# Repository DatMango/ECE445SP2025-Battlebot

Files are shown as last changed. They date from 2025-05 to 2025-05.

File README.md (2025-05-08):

# ECE445SP2025-Battlebot
UIUC ECE 445 Spring 2025 - Senior Design Repository

## Project: Ant-weight, 3D Printed Battlebot
Name of Battlebot: Ant-weight Battlebot - Scooper

<p align="center">
    Scooper Image
</p>

## Team Members:
- Justin Leong (jyleong2@illinois.edu)
- Yuxuan Nan (yuxuann2@illinois.edu)
- Zilong Jiang (zjian4@illinois.edu)

## TA:
- Bill Yang (hy38@illinois.edu)

## Problem
The issue at hand is an Ant-weight, 3D Printed Battlebot Competition in which each team wants to win. There are certain constraints of the Battlebots’ design in order to be eligible and win. To win the competition, the goal of a battlebot is to outlast or destroy the opponent team’s battlebot. Different teams will have different designs, meaning a battlebot designed for winning must take into account as many factors to withstand and outlast the competition.

## Solution
We decided upon developing a 3D Printed Bluetooth-controlled battle bot powered by an ESP32 microcontroller. The Battlebot communicates with a PC via a Bluetooth module, enabling wireless command and control. It is equipped with two DC motors driven by H-bridge circuits for precise movement and a ramp-shaped weapon system for engaging in battles. The ESP32 manages motor control using GPIO and PWM, while the weapon system utilizes GPIO. The bot integrates real-time communication, robust motor control, and weapon functionality, offering an engaging and functional design. My goal is to create a responsive and competitive robot for dynamic competitions.

## Lab Notebook
[Can be found here!](Documentation/Notebook.md)

## Video!
[Battlebot Intro Video](https://youtu.be/LQH7uXVlK6E)

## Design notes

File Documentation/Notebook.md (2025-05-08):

# Lab Notebook
For weekly entries of what occurred in design.

Our weekly meetings with our TA, Bill Yang, were on Mondays 6-6:30PM.

### Final Design
<p align="center">
    Final Battlebot Image
</p>

# Week of Jan 20
The beginning of the school year, formed group of: Justin, Yuxuan, and Zilong. This was the week of the Initial Web Board Post. Also when we decided on the idea of partaking in the Antweight, 3D Printed Battlebot competition hosted by Professor Gruev.

# Week of Jan 27
Our group solidifed of taking the Antweight Battlebot competition, and created our Early Project Approval to turn in 1/29. Everyone worked together to make sure to include the necessary details for the Early Project Approval ([Early RFA](Early%20RFA.md)). Also the week of the CAD assignment.

# Week of Feb 3
After third class meeting, we confirmed together that we were working on the Antweight Battlebot. Also were confirmed to be the first group to be approved - hence became Group 1. We began working together on the Project Proposal.

# Week of Feb 10
This week contained our first meeting with our TA (Bill). Beforehand, we as a team had prepared and worked on a first draft of our Block Diagram, three High-Level Requirements, and one Subsystem Requirement from our worked on Project Proposal. We had seeked feedback from Bill upon our project and got some guidance in the right direction on how to develop a Pneumatic system. We also sought advice on if we were in the right direction for our Project Proposal. This was also the week we turned in our [Project Proposal](Project%20Proposal.pdf) as well as our [Team Contract](Team%20Contract.pdf). Finally, we made sure that our Project Proposal was ready for the Proposal Review.

### Images
<p align="center">
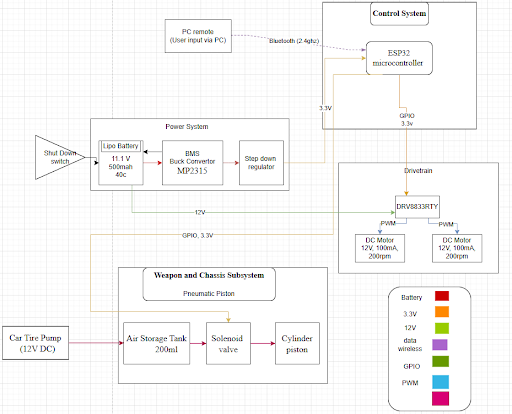
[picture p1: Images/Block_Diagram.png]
Final Block Diagram
    
</p>

# Week of Feb 17
No weekly meeting with Bill this week. There would be a Design Review of our Project Proposal. Design Review would take place on 2/19 11AM. I believe there was an update to our high level block diagram a day before the review due to some missing parts.

### Tasks
- Everyone focuses on making sure [Project Proposal](Project%20Proposal.pdf) was ready for the Project Proposal / Design Review.
- Begin on working on PCB schematics.

# Week of Feb 24
Our weekly meeting with our TA is now Mondays 6-6:30pm. Feedback from Bill for this week was primarily about looking at our PCB schematics but this was when we had the STM32. Partial of the STM32 wiring can be found in the images section. We also did ask about changing from STM32 to ESP32 but this would later be done after the PCB Review. After the PCB Review, we were told that we were allowed to change from STM32 to ESP32. The STM32 we had originally picked did not support Bluetooth or WiFi communications, additionally, we found the ESP32-WROOM-32E to be easier to work with and supported all of our needs. We would also try to finish the PCB files before the first round PCBway orders. We also began working on the Design Document. Towards the end of the week after deciding to swap to the ESP32, we also began figuring out how to code for the ESP32 using WiFi signals as originally (Justin) thought that WiFi would be more instant than Bluetooth. However, later on we learned the actual difference between Bluetooth and WiFi is quite minimal for these kinds of projects in comparison to things that require 2.4Ghz connections (i.e. Gaming/Reaction based projects).

### Images
<p align="center">
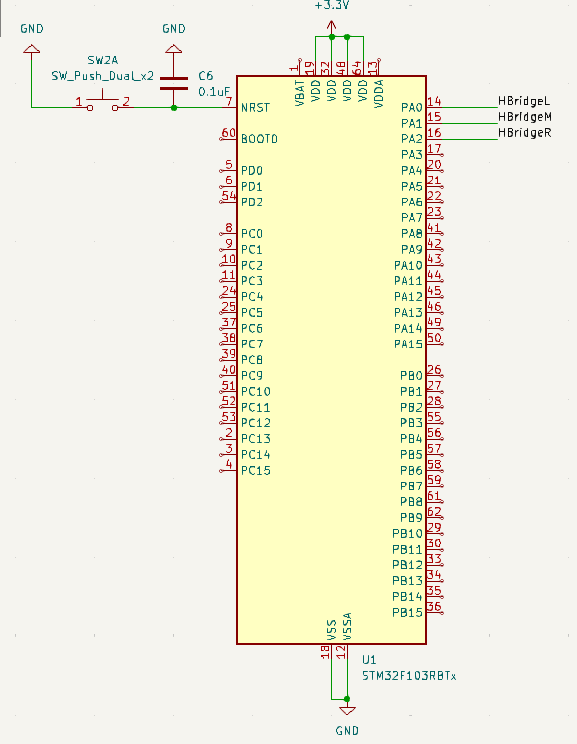
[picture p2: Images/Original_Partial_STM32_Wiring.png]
Partial STM32 Wiring
    
</p>

### Tasks
- Everyone begins working on PCB schematic and layout
- Everyone Research parts (datasheets) required for system to better understand PCB
- Everyone also work on the Design Document
- Zilong will be focusing on researching Pneumatics and schematics
- Justin and Yuxuan will be focusing on the software/programming of the ESP32, test on dev kit

# Week of Mar 3
Unfortunately, we did not finish all of the PCB schematics before the first round PCBway orders which was due during our TA meeting. This was primarily due to having to rewire components and read the datasheet of the ESP32 we picked. However, we did ask Bill more in depth questions about if what we were doing for our schematics and PCB design were good or not. We got feedback of how we could utilize the datasheets of components to easily wire everything. In terms of coding a frontend, we also asked Bill on some advice with coding our controller on PC using things like the Python library Tkinter and other frontends. During this week, we all also had to work on and turn in the [Design Document](Design%20Document.pdf). For the Design Document, also decided that we wouldn't use a step down regulator as the Buck Converter was able to change the 12V to 3.3V voltage on its own safely. Finally, Justin and Yuxuan would get ready for the Breadboard Demo by programming the ESP32 and connecting to our PC (as controller) over WiFi (hotspot) and getting some signals to work.

### Tasks
- Everyone prepare for Breadboard demo
- Everyone will work together on PCB design, primarily Zilong 
- Everyone finish the [Design Document](Design%20Document.pdf)
- Everyone get ready to order parts (pick and choosing), Yuxuan will handle most of the ordering
- Justin and Yuxuan focus on getting the ESP32 programmed (using WiFi) with a frontend controller on PC

# Week of Mar 10
No weekly TA meeting this week. For the Breadboard Demo, we were able to get a version running where we could send either 1 or 5 signals to our ESP32 and get outputs (LEDs) on the breadboard to work. However, the 5 signal version didn't work very well. From the Breadboard demo with Professor Gruev and TA Bill, we were told that we were a bit behind schedule (compared to other teams). Additionally, this was when Professor Gruev helped us make the decision of switching back from WiFi to Bluetooth because there were still secure connections over Bluetooth and reduces points of failures. 

We also finished our first revision of our PCB for the second round PCBway orders. We made sure to design our PCB utilizing the datasheets of components. Important components like the LM2596S-3.3 buck converter, power switch, ESP32-WROOM-32E microcontroller, DRV8833RTY H-Bridge module. Converted to [Gerber V1](../PCB/Gerber%20V1/) files. We also started purchasing some components.

For the coding portion: Essentially, we used a hotspot (WiFi) as our method of wireless communication for this week as it seemed more instant. Additionally, we chose hotspot due to some restrictions from the school's internet. Furthermore, we were able to get our Devkit to connect to our hotspot and computer, thus allowing for signals to be sent back and forth. We designed an interface with 5 on-screen buttons (on/off) that were mapped to specific GPIO pins (programmed) through Arduino IDE. To make sure we were sending signals properly, we connected LEDs to each of the GPIO pins programmed to see whether they could be turned on/off. The 1 version button was fine, but when changing to 5 buttons, there were some weird issues with it that we attempted to debug.

### Tasks
- Justin and Yuxuan primarily focus on getting programming done for the Breadboard Demo
- Everyone focus on getting in our PCB Design in for PCBway orders, everyone helps with schematic
- Zilong will get the PCB layout designed with assistance from Yuxuan

### Notes
- Code that we utilized for this Breadboard demo can be found in [Old Code, connected utilizing WiFi/HotSpot](../Code/Original%20Code%20(Not%20Working)/)
- The portions of our original PCB design that we used can be found in [Design Document](Design%20Document.pdf). The actual Gerber files (that we still have) can be found in [PCB Gerber Rev 1 Files](../PCB/Gerber%20V1/)
- An example of issues we ran into for our Revision 1 PCB is in the Images

### Images
<p align="center">
    Rev1 PCB Error
</p>

# Week of Mar 17
The week of spring break. Attempt to get back on schedule if time. Ordered some components. Found Dabble library to utilize for controller (on Phone) and connect to the ESP32.

### Tasks
- Everyone if time, do what we can to get back on schedule
- Justin and Yuxuan find software changes if time

# Week of Mar 24
During our weekly TA meeting, we got some advice on 3D printing (i.e. what software to use). Additionally we got some advice on our PCB on components, programming the chip, etc. We also got more advice on Pneumatic system. In this week, we began playing around with 3D prints to see what our Battlebot would need in size, etc. More importantly, Second Round PCBs arrived. However, after attempting to test, we figured out that the board wouldn't have worked properly. This was because in the original schematic wiring, (Justin) didn't realize that labeling a wire "12v_out" and KiCad's "+12V" label are different, which thus made virtually anything connected to the +12V wire not powered. As such, we had to fix this for third round orders. We also sized down our board to make it more compact. Made many more adjustments to the PCB in general - including programming pins, Pneumatic placeholder, rewiring certain pins - this version can be found in [PCB V2](../PCB/group1_battlebot/). Also, Justin and Yuxuan made lots of progress for the software portion, only needs minor changes (if any). Finally, Zilong made a first version of his Pneumatic system with some testing.

### Tasks
- Zilong will focus on 3D prints, Yuxuan will also help work on this
- Zilong work on Pneumatic system with help from Yuxuan
- Justin and Zilong fix PCB
- Justin and Yuxuan work with Dabble library coding

### Images
<p align="center">
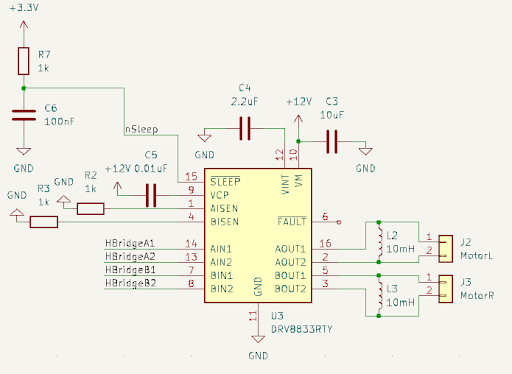
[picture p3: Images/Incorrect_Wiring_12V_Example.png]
Incorrect 12V Wiring
    
</p>

<p align="center">
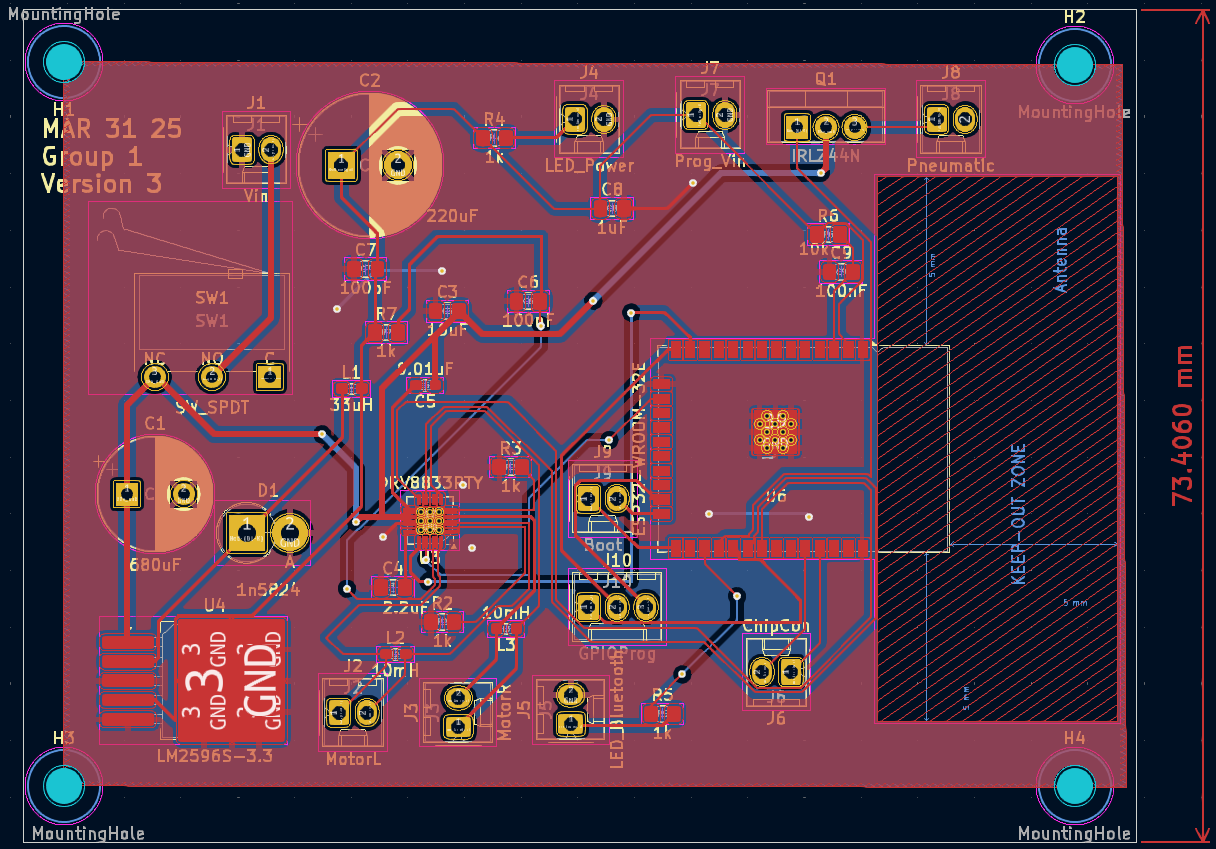
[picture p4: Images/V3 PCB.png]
PCB V2
    
</p>

### Notes
- Code created can be found in [Final Code](../Code/Working%20Code/). How it's used can be found in [Code Information](../Code/Important_Code_Info.md)

# Week of Mar 31
During our weekly TA meeting, we mostly demoed the Pneumatic system working utilizing the power supplies (I believe at this time it was running using NMOS transistors for the demo with Bill). Also during this meeting, we ordered the 3rd round PCBs. The advice we got mostly related to the Pneumatic system in this week on how to keep it together and related information that we kept in mind. This week was mostly testing some components that we could on the 2nd round board. Zilong also was trying to find the correct NMOS for the Pneumatic system.

### Tasks
- Everyone prepare for 3rd round PCBs (components)
- Justin and Yuxuan any last minute software changes
- Zilong changes with 3D prints
- Everyone some testing with components we had

# Week of Apr 7
The weekly TA meeting, we ordered more components. We also demoed the Pneumatic system working a bit more consistently as well with the piston with more "firepower". Ultimately, the Pneumatic system was a bit more air tight than the previous week and was more consistent in firing/attacking. This may also have been the week Zilong transitioned from the NMOS to BJT such that it was activated based on current rather than voltage. In this week, the third round PCBs arrived - our revision two. For the most part, we were soldering on components and unit testing the different subsystems to verify they worked. We did struggle with the hot air gun and hot plate at first, sometimes applying too much heat and burning some chips. We were also informed of the reflow oven for using solder paste instead which would make our lives easy later on.

### Tasks
- Everyone work on soldering and Unit testing components
- Zilong continue to work on 3D prints
- Zilong modify the Pneumatic system as required
- Justin and Yuxuan be ready for changes to software

### Images
<p align="center">
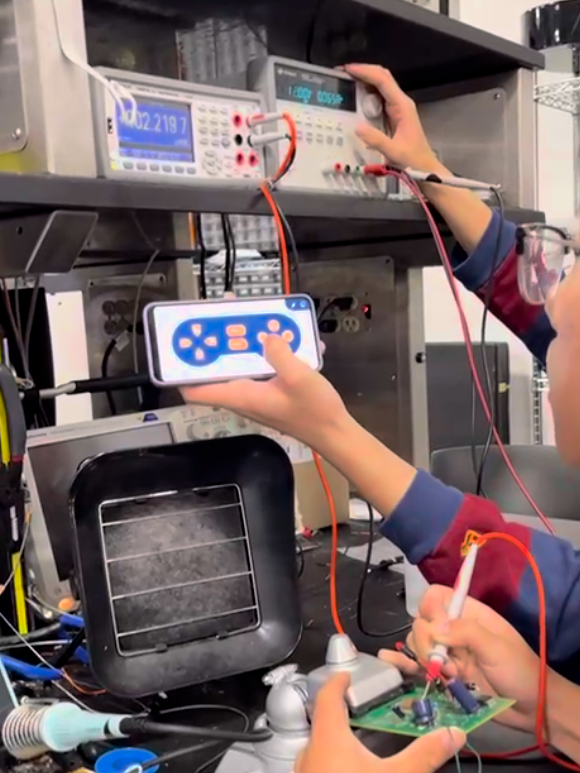
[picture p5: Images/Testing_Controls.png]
Testing Controls
    
</p>

# Week of Apr 14
During this weeks weekly TA meeting, we demoed the Pneumatic System working more reliably. Addiitonally, we finally triggered it using the ESP32 dev kit control signal. By this point, Zilong had changed the Pneumatic system to use a BJT instead of NMOS. Zilong also needed a slightly altered circuit to reliably trigger the Pneumatic system. He utilized the TIP120 BJT chip, added in things like a flyback diode, and have a 10k-ohm resistor between the microcontroller and the base of the TIP120 to limit current draw. This made the Pneumatic system a lot more reliable in triggering. Besides this, everyone continued to work on soldering, unit testing, and debugging our circuit. Test the parts according to the design/verification as found in [Design Document](Design%20Document.pdf).

### Tasks
- Everyone continue to solder, unit test, and debug circuit
- Zilong continue working on Pneumatic
- Zilong continue to work on 3D prints

### Images
<p align="center">
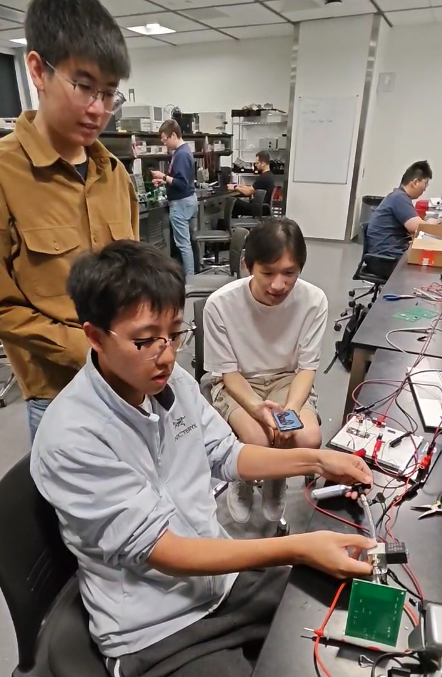
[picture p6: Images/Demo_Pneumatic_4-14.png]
    
</p>

# Week of Apr 21
In the weekly TA meeting with Bill, we were to perform our Mock Demo. We were able to demonstrate full functionality of the individual subsystems. The control and weapon subsystems (power subsystem was a bit harder to show) we were able to demonstrate easily. The drivetrain subsystem was a little bit more difficult as we had to figure out why the chip itself wasn't working properly; we were able to show that the actual code was correct for directional inputs and activating Pneumatic weapon. Finally, we realized that the H-Bridge (DRV8833RTY) was wired (somewhat) incorrectly. The DRV8833RTY VM's pin only supports a max of 10.8V but we were giving it 12V (11.1V+) from the battery/power supply. We diagnosed this by checking the nFault pin which would read logic level low when there is a faulty condition. As such, the only possible reasons were because we had fried the chip or burnt it (from the reflow oven). It was most likely due to giving a higher voltage than it could handle. 

We had to make the difficult decision of utilizing a separate PCB H-Bridge module because it was too hard to rewire values for another H-Bridge and it was also too late to order a new PCB. The H-Bridge we went with was the L9110s driver. It essentially functions the same as the DRV8833RTY but it can support the 12V that we needed.

We also began 3D printing the final versions of our chassis and weapon (scooper). We also got the final revisions of our circuit soldered together and assembled everything together into the Battlebot. Mount things like the Pneumatic System, drivetrain, weapon, PCB to the lid for space management. This is probably the time (Justin) charged the battery using power supply (felt really sketchy/wrong just connecting wires into the battery, but still worked). We also performed testing/verification on the different components. All testing results can be found in [Final Presentation](Ant-weight%203D%20Printed%20Battlebot%20slides.pdf) or [Final Report](ECE%20445%20Final%20Report.pdf).

### Tasks
- Everyone prepare for Final Demos, make sure circuit works as intended
- Everyone get final 3D prints ready - [3D Print Materials](../3D_Print/)

### Notes
- I think this was the week we extended the tube length of Pneumatic system for more power.

### Images
<p align="center">
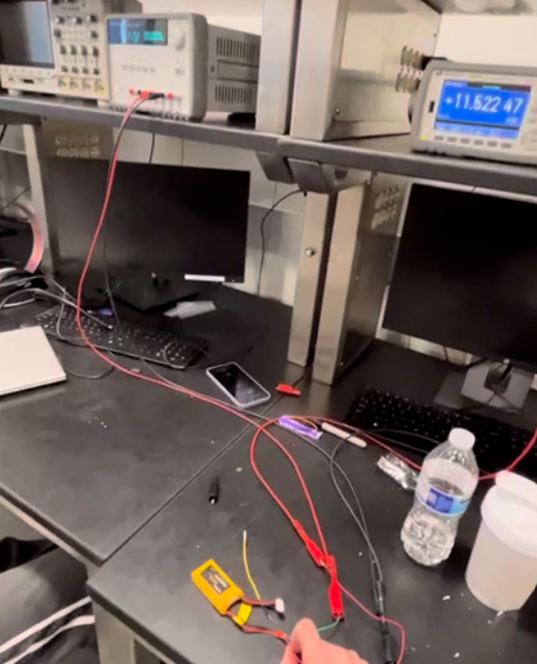
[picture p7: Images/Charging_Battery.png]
Internal Image
    
</p>

# Week of Apr 28
No weekly TA meeting (I think?). This was the week of Final Demos and Mock Presentations. We had a fully working Battlebot with all our specifications ready on Monday. Minutes before the actual Final Demo on 4/28, we somehow managed to fry the Buck Converter, which then fried our ESP32 (tested using voltmeter/multimeter). Luckily, Professor Gruev was kind enough to allow us to Demo on Wednesday. We overnight shipped a new buck converter (LM2596S-3.3) from Digikey and resoldered everything onto a new board (with a new ESP32) and reprogram it. We then electrical taped the inside of our Battlebot for any components we suspected could somehow accidentally cause short circuits or touch other components. We successfully made the Final Demo, Battlebot pictures and more in depth can be found in [Final Presentation](Ant-weight%203D%20Printed%20Battlebot%20slides.pdf). Also had mock presentations this week which we used to then enhance our Final Presentation to what it is now.

### Tasks
- Everyone get ready for Final Demos, make sure board is working
- Everyone prepare/finish [Final Presentation](Ant-weight%203D%20Printed%20Battlebot%20slides.pdf) (for both Mock and Final Presentation)
- Everyone get ready to present the Final Presentation
- Also performed Extra Credit Video Assignment [Extra Credit Video](https://youtu.be/LQH7uXVlK6E)

### Images
<p align="center">
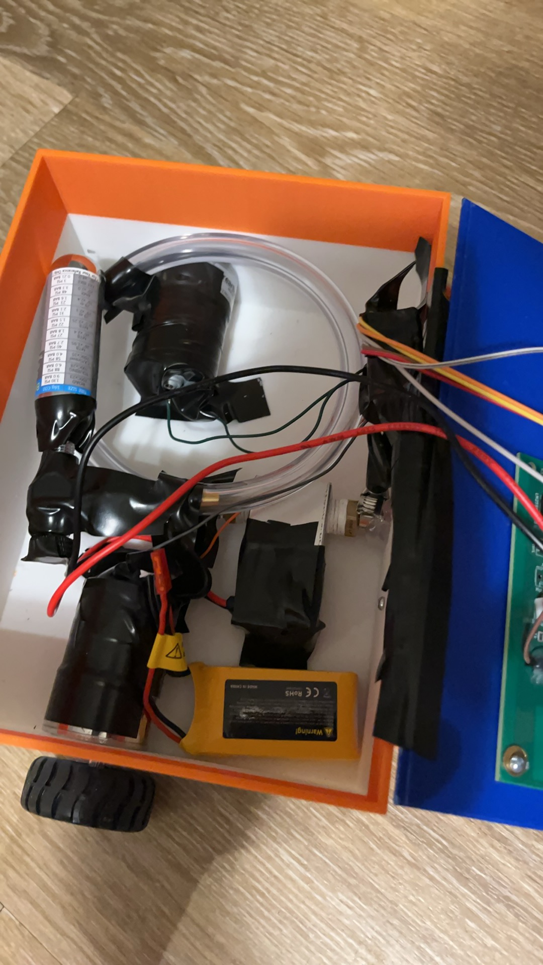
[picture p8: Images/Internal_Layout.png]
Internal Image
    
</p>

### Notes
- All 3D prints can be found in [3D Print Materials](../3D_Print/)

# Week of May 5
No weekly TA meeting. We all worked on the [Final Paper](ECE%20445%20Final%20Report.pdf) after the Final presentation. Also worked on the Lab Notebook together and getting everything pushed to our GitHub repo.

### Tasks
- Everyone perform [Final Presentation](Ant-weight%203D%20Printed%20Battlebot%20slides.pdf)
- Everyone finish Final Paper
- Everyone finish Lab Notebook

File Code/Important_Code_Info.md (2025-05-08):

# Important Use of Code
All relevant code for the final battlebot is located in working code. Please note that I have included our updated DabbleESP32 library due to it being meant for an older version of ESP32s.

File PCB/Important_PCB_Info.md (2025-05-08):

# Important Use of PCB
All of the latest battlebot PCB files are located in group1_battlebot.

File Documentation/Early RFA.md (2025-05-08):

# Ant-weight Battlebot - Scooper

# Group members
- Yuxuan Nan(yuxuann2)
- Justin Leong (jyleong2)
- Zilong Jiang(zjian4)

# Problem
The issue at hand is an Ant-weight, 3D Printed Battlebot Competition in which each team wants to win. There are certain constraints of the Battlebots’ design in order to be eligible and win. To win the competition, the goal of a battlebot is to outlast or destroy the opponent team’s battlebot. Different teams will have different designs, meaning a battlebot designed for winning must take into account as many factors to withstand and outlast the competition.

# Solution
We decided upon developing a 3D Printed Bluetooth-controlled battle bot powered by an STM32 microcontroller. The Battlebot communicates with a PC via a Bluetooth module, enabling wireless command and control. It is equipped with two DC motors driven by H-bridge circuits for precise movement and a ramp-shaped weapon system for engaging in battles. The STM32 manages motor control using GPIO and PWM, while the weapon system utilizes GPIO or I2C protocols for activation. The bot integrates real-time communication, robust motor control, and weapon functionality, offering an engaging and functional design. My goal is to create a responsive and competitive robot for dynamic competitions.

# Solution Components

## DriveTrain
The drivetrain of our battlebot will utilize two DC motors with high torque to power two of our rear wheels making this a rear wheel drive robot. We have decided upon a brand of motor that will output 0.58kgf.cm of torque as well as have a max of 200 RPM in rotational speed. The rear wheels will consist of high-friction wheels that allow for lots of traction to handle the speed. Additionally, we will combine this with an omni-directional front wheel to allow for easy directional movement if the weight capacity allows it. Furthermore, we will combine this with an H-bridge circuit to allow control, stability, and power for the battlebot.

## Weapon and Chassis
The weapon and chassis are required to be 3D printed according to the list of approved plastic types. Ideally if possible, we would like to use ABS plastic as this would be the best in terms of weight and durability but have opted for PLA+ plastic as it is easier to print designs. PLA+ plastic also offers decent strength and isn’t as brittle as the other provided plastics. For weapon design, we will be creating a Skid Bucket type weapon that can potentially be moved up and down using pneumatics to attack other battlebots (both for ramming and slamming other battlebots). In terms of chassis, we have decided to use two motors for rear wheel drive box-ish battlebot as well as an omni-directional front wheel to make steering easy.

## Power system
In the power system module, this includes regulators and converters to different electronics, the battery, and a monitor for the battery with a switch/relay. For the battery, we have decided upon a 12V NiMh battery as this can supply consistent and reliable power. We will also include a short circuit detection that will turn off the battery for safe practice.

## Control system
The control system will be powered by an STM32 microcontroller, which will manage motor control and wireless communication. Using a Bluetooth module, the bot will communicate with a PC, enabling real-time control with minimal latency. The STM32 will leverage GPIO and PWM to provide precise speed and directional control for the motors, ensuring responsiveness and accuracy during battles.

# Criterion For Success:

Our battlebot would be considered successful if we can control the battlebot via Bluetooth relatively well. This would include having both motors work separately for steering as well as being able to make each motor have different amounts of throttle inputted. Additionally, we would like our weapon to work well enough to be considered functional during a match.

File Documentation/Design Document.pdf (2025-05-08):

# ECE 445 Spring 2025 Senior Design Document

# Project #1: Ant-weight, 3D Printed Battlebot

# Team Members: Yuxuan Nan(yuxuann2) Justin Leong (jyleong2) Zilong Jiang(zjian4)

# TA: Bill Yang Professor: Viktor Gruev

# 1. Introduction

## Problem

In the Ant-weight 3D Printed Battlebot Competition, designing a robot that is both strong and lightweight is a big challenge. The robot needs to have enough power to move quickly and use its weapon effectively, but at the same time, it cannot be too heavy. A heavier bot might be stronger, but it will use up the battery too fast. On the other hand, if the bot is too light, it might break easily during battle. Finding the right balance between battery life, weight, and material strength is important to make sure the bot lasts the full match while staying durable.

Another key problem is Bluetooth communication. The robot must receive real-time commands from the controller without any delays or connection problems. However, in a competition setting, many robots are using Bluetooth at the same time, which can cause signal interference and slow response times. If the bot does not react quickly to commands, it could be at a big disadvantage. To build a competitive Battlebot, we must make sure the Bluetooth connection is fast and stable, even in a crowded environment.

## Solution:

To solve these challenges, we are designing a 3D-printed, Bluetooth-controlled Battlebot that balances strength, weight, and power efficiency. The chassis will be made from PLA+, which is stronger than regular PLA but still lightweight, helping the bot survive impacts without being too heavy. The battery is carefully chosen to provide enough power for the whole match while keeping the bot within the weight limit. The motors are controlled using PWM signals, allowing for smooth movement and quick direction changes while using power efficiently.

For better wireless control, we are using the ESP32-WROOM-32E module, which supports fast and stable Bluetooth communication even in environments with many signals. This will reduce delays when sending commands, making sure the bot reacts quickly. The weapon system uses a pneumatic flipping mechanism with a controlled air pressure system, allowing for powerful but efficient attacks. Together, these improvements ensure our Battlebot is durable, fast, and responsive, making it highly competitive in the Ant-weight class.

## Visual aid:

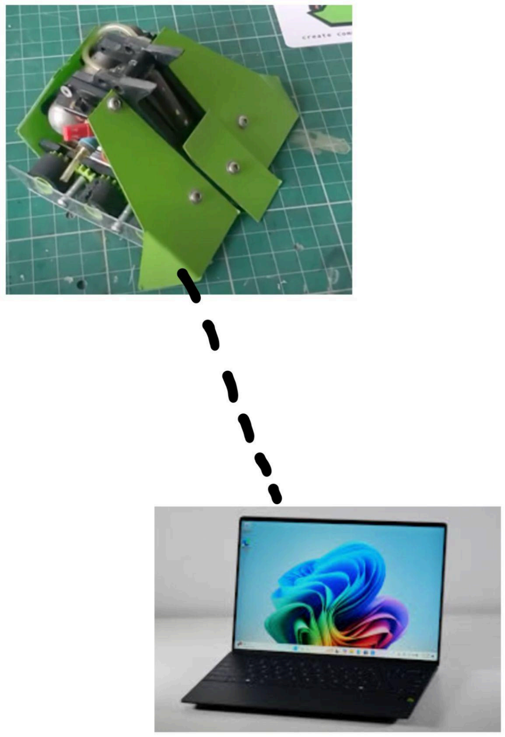
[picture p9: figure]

Our Bluetooth-connected Battlebot will be controlled using a computer-based interface, where movement commands are sent wirelessly through the ESP32-WROOM-32E module with minimal delay. The control scheme will be simple and intuitive: pressing "W" moves the bot forward, "S" moves it backward, "A" turns it left, and "D" turns it right, allowing for precise maneuverability. Additionally, pressing the spacebar will activate the ramp-flipping mechanism, enabling strategic attacks during battle. This setup ensures smooth and responsive control, giving the operator the ability to quickly adapt to the competition and make real-time decisions.

## High level require list

1> The Battlebot must be wirelessly controlled via Bluetooth, ensuring smooth and real-time command execution without huge delay.
2> The chassis must be strong yet lightweight, using PLA+ 3D-printed material, capable of withstanding high-impact collisions.
3> The weapon system must function reliably, utilizing a pneumatic flipping mechanism with a controlled air pressure system that allows at least one successful flips per charge without performance degradation.

# 2. Design

## Block Diagram:

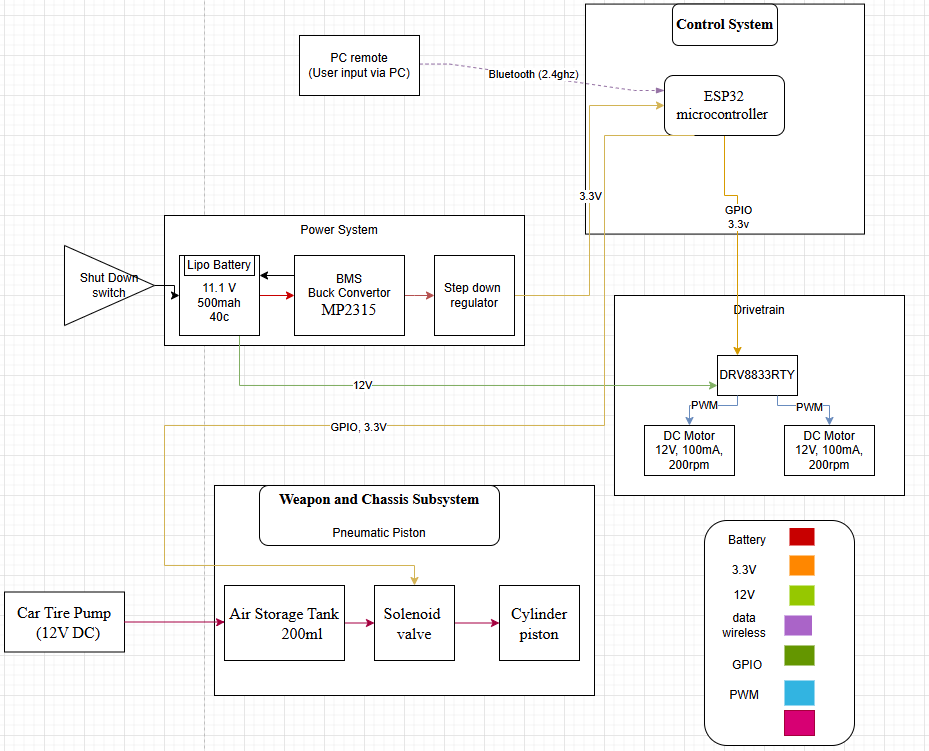
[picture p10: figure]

## Subsystem Drivetrain

The drivetrain is responsible for the Battlebot’s movement and maneuverability. It utilizes two high-torque DC motors from Greartisan, which each provide 2.2 kg⋅cm of torque and a no-load speed of 200 RPM. These motors drive the rear wheels, enabling precise movement with enhanced torque for pushing against opponents. The motors are controlled via an H-bridge from Texas Instruments (DRV8833RTY), allowing bidirectional movement and speed control with improved efficiency. The circuit ensures the motors can dynamically adjust speed and direction for quick and strategic maneuvers. The battlebot employs PWM (Pulse Width Modulation) signals from the ESP32 microcontroller, ensuring variable speed control with smooth acceleration and deceleration.

The rear wheels are equipped with high-friction tires to maximize traction, enabling the bot to push against opponents effectively. The front wheel is omni-directional, ensuring smooth directional changes and enabling pivoting maneuvers. This combination optimizes the bot’s agility and defensive capabilities while maintaining stability during combat.

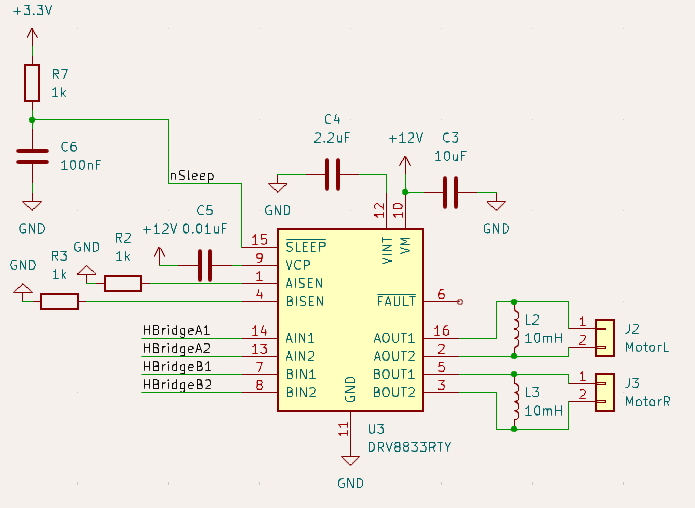
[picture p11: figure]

Subsystem Requirements and Verifications:

- Each motor can roughly produce the a maximum of 2.2kg * cm amount of torque under no load per the motor’s specifications; this will be tested in practicality by it being able to push something of approximately 2.2kg for about 1cm
- Each motor can reach a maximum of 210 rpm with no load, the upper limit of the motor providing no burnout conditions; this can be “simple” tested by taping something to the shaft (light) and seeing if it spins. The less we can see the paper flying about, the faster it is. With accurate tool measurements, (if provided) we can use a tachometer or strobe light with calculations to calculate the actual speed. Otherwise, we can test the RPM when actually accelerating the robot with wheels and calculating based on time, distance, and wheel diameter

## Subsystem Weapon and Chassis

The primary weapon is a Pneumatic Ramp Flipper, specifically designed to flip opponents with precision and efficiency. It features a low-profile, angled ramp that smoothly slides underneath for effective lifting. The system operates using a pneumatic actuator connected to a 200ml gas tank pressurized at 120 PSI, enabling controlled solenoid valve activation for each flip.

Pneumatic Control System
The solenoid valve is precisely controlled by an ESP32 microcontroller, ensuring exact timing for activation. The system utilizes a transistor-based switch to handle the 11.1V power supply required by the solenoid: A logic-level N-channel MOSFET is used to switch the solenoid valve on and off. NMOS is used to trigger low side, as the gate is powered, it will allow the current pass through to ground.
- Gate: Connected to the ESP32's GPIO pin (3.3V logic).
- Drain: Connected to the solenoid’s negative terminal, which is powered by the 11.1V battery.
- Source: Connected to ground.
When the ESP32 outputs HIGH (3.3V), the MOSFET conducts, activating the solenoid and opening the valve to release air and flip the opponent. When the ESP32 outputs LOW (0V), the MOSFET turns off, closing the valve and stopping airflow. A pull-down resistor (1kΩ) ensures the MOSFET remains off when no signal is present, preventing unintended body leakage.
Pressure & Flow Regulation
To maintain consistent flipping power while conserving air, a pressure regulator ensures even pressure distribution to the pneumatic actuator. Additionally, manual flow control valves allow for safe pressure release when needed. The compact air tank is optimized to support up to 5 flips per charge before the pressure reduces, ensuring efficient battle performance.

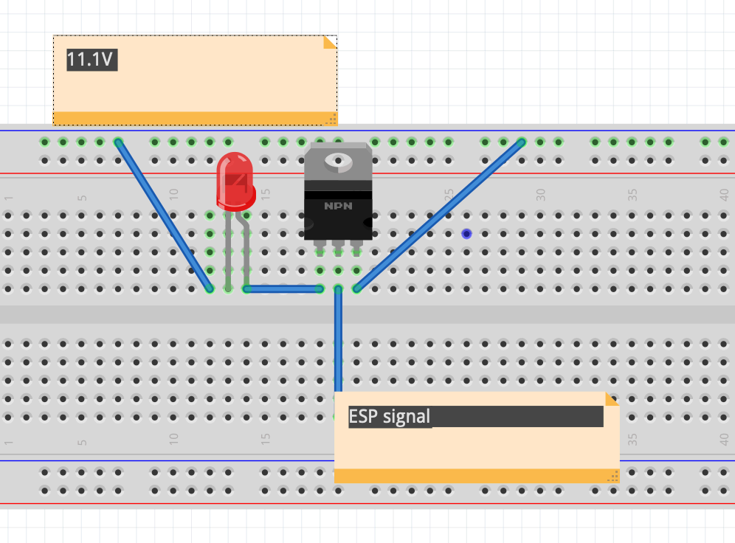
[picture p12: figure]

The chassis is 3D-printed using PLA+ plastic, which offers a balance between durability and weight efficiency. PLA+ is selected over standard PLA due to its increased impact resistance and reduced brittleness. The chassis design features structural reinforcements in high-stress areas, ensuring it can withstand repeated impacts without compromising integrity.

The low center of gravity of the bot further improves stability, preventing easy flipping by opponents. Additionally, weight distribution is optimized to ensure consistent movement and controlled aggression during combat.

Subsystem Requirements and Verification:
- Have a solid building structure of PLA+ plastic that can withstand the force of ramming 2lbs; this can be tested by using something of roughly 2lbs to put in the way of the battlebot
- Have a gas tank that can withhold 120psi for the weapon; this will be shown and tested through the pressure gauge attached to the system to check for holding capabilities

## Subsystem Power System

The power system ensures consistent and reliable power delivery to all components. A 3S 11.1V 500mAh LiPo battery (Flex Innovations, 2025) provides power to the drivetrain, control, and weapon subsystems.

The Greartisan motors operate within a 6V-12V range, and since a fully charged 3S LiPo battery outputs 12.6V, the system can efficiently power the motors without additional voltage regulation. The battery voltage will naturally decrease during operation but will remain within the acceptable range.

A voltage monitoring circuit is integrated to track power levels and ensure the motors do not receive excessive voltage beyond their rated limits. The power system also includes overcurrent and short-circuit protection mechanisms, ensuring safety in case of electrical faults.

To supply lower voltage components such as the ESP32 microcontroller and sensors, a step-down (buck) voltage regulator is used to convert the 11.1V battery output to stable 5V and 3.3V power. This ensures efficient and heat-minimized operation, preventing excessive power dissipation that would occur with a linear regulator. The regulated voltage allows stable operation of logic-level electronics while maintaining overall energy efficiency.

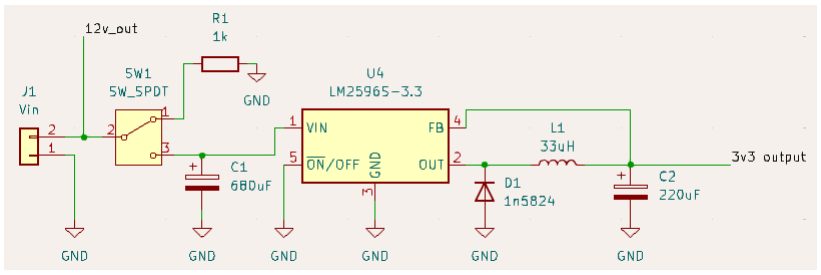
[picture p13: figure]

Subsystem Requirements and Verification:
- Can supply a continuous 3A of current to all subsystems when under load (Check Tolerance Analysis). This can be formally measured through a multimeter on the current setting.
- Have enough capacity to last 2 minutes of continuous usage to last the battle (our current battery is 500mAh). The most accurate way to test this would be timing our system using a timer when the battlebot is turned on.

## Subsystem Control System

The ESP32-WROOM-32E microcontroller serves as the central processing unit of the Battlebot, handling real-time control inputs, motor operation, and weapon activation. The microcontroller is programmed to interpret Bluetooth commands from a PC controller, ensuring precise movement and attack execution.

The control system leverages PWM for speed modulation, GPIO for directional control and communication for sensor data (if applicable). The microcontroller processes commands with a response time of under 100ms, ensuring low-latency execution during battles.

The Bluetooth module is optimized for high-speed, interference-free communication, ensuring real-time command execution without signal drops. Extensive testing is conducted to mitigate latency issues and improve responsiveness.

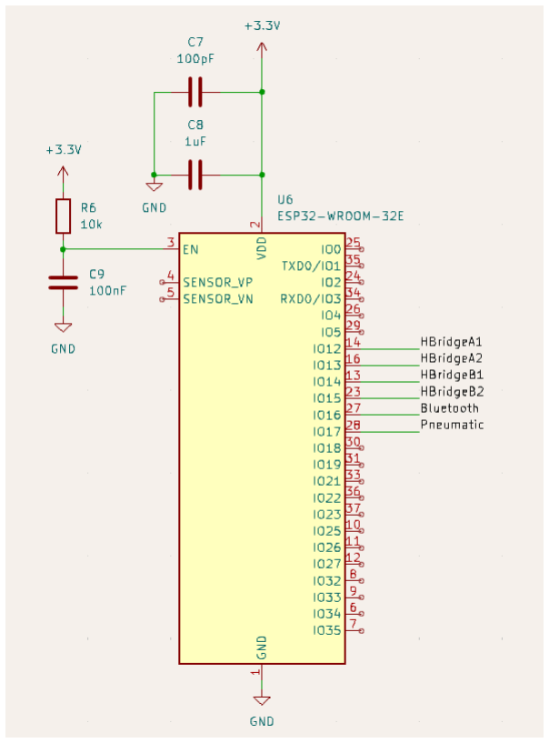
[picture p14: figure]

Subsystem Requirements and Verification:
- Be able to connect via bluetooth from the computer we intend to use as a remote to our ESP32 microcontroller and control/send signals to the different subsystems. This can be tested when our ESP32 is receiving and demonstrating inputs from our computer. Additionally, we will have an LED to display if connected via bluetooth.
- Be able to control the direction of the battlebot with given signals. To demonstrate this, we will show the motors being able to spin in different directions when the controls indicate a turning movement.

## Tolerance Analysis

An aspect of our design that may pose a threat to the successful completion is if our battery depletes before the end of the 2 minute time limit with the assumption that it is an endurance fight. In order to counteract this, we have decided to find a battery that will supply enough voltage to the different components while also having enough amperage such that it can sustain throughout the whole fight with extra power to spare.

To calculate the amount of amperage required of our battery, we need to calculate the power usage of all the subsystems based on a given time.

The motor we selected (at 12V) has a max efficiency of 0.1A draw with a 2A stall current.

Average and Peak Current Draw of both motors:
Imotors = Nmotors * Imotor = 2 * 0.1A = 0.2A

IpeakM = Nmotors * Imotor_peak = 2 * 2A = 4A

Our Pneumatic system has a rough average current draw of 3A with a peak current draw of 5A. Additionally, our ESP32 and related components have an average current draw of 0.15A and a peak current draw of 0.2A.

The calculation of how much our battery capacity need as well as tolerance can be calculated as follows:

Total and Peak Current Draws:
Itotal = Imotors + Ipneumatic + IIC = 0.2A + 3A + 0.15A = 3.35A

Ipeak = Imotors_peak + Ipneumatic_peak + IIC_peak = 4A + 5A + 0.2A = 9.2A

Capacity of Battery Wanted = Itotal

* Total Time = 3.35A * 2min = 3.35 * 2/60 h = 0.1116 Ah Peak current of battery = 9.2A

Because actual consumptions with batteries will vary, we need to make sure that the battery can handle 9.2A of peak load draw as well as have a total capacity of at least 0.1116Ah. This will ensure that the battery can handle the components we are using as well as last the total battlebot round of 2 minutes. The battery we have opted for has a capacity of 500mAh - which satisfies the capacity of battery wanted by a lot to ensure even with not optimal conditions it will work - as well as discharge rate of 35C and max discharge rate of 70C. To ensure that the peak current and current ratings are within this discharge rate, we take the amperage divided by the total capacity of the battery (3.35A/500mAh = 6.7C and 9.2A/500mAh = 18.4C), both of which are within limits: 6.7C < 35C and 18.4C < 70C.

# 3. Cost and Schedule

## Cost Analysis:

The total cost of the project consists of labor costs and parts costs required for the development and assembly of the Battlebot. Our team consists of one Electrical Engineering student and two Computer Engineering students, each contributing 60 hours to the project. Based on recent salary estimates for ECE graduates from the University of Illinois, we assume an hourly rate of $40 for the EE student and $38 per hour for each CE student. The total labor cost is calculated as $40 × 60 = $2,400 for the EE student and $38 × 60 = $2,280 per CE student, resulting in a total labor cost of $6,960 for the team.

In addition to labor, the project requires various electronic components, mechanical parts, and structural materials, as listed in the budget document. This includes the ESP32-WROOM-32E Bluetooth module, high-torque DC motors, 3D printing materials (PLA+ filament), a LiPo battery, and pneumatic system components for the weapon mechanism. The total cost of these parts, calculated from the latest budget list, amounts to $7200
Combining labor and parts costs, the total estimated cost for the project is $7350, ensuring that all subsystems, including control, power, drivetrain, and weapon systems, are fully developed and tested within budget constraints

## Schedule:

Include a time-table showing when each step in the expected sequence of design and construction work will be completed (general, by week), and how the tasks will be shared between the team members. (i.e. Select architecture, Design this, Design that, Buy parts, Assemble this, Assemble that, Prepare mock-up, Integrate prototype, Refine prototype, Test integrated system).

Week | Checklist
3/10 | Pass audit check and order pcb
3/24 | Soldering parts together, and check if bluetooth connect properly
3/31 | Buy the pcb again if the first pcb does not work and use 3d printer to print out battle bot
4/7 | Solve the pneumatic system and make sure it is work
4/14 | Assemble all parts together
4/21 | Final check

# 4. Discussion of Ethics and Safety:

Ethical Considerations
Our project adheres to the IEEE Code of Ethics (IEEE, 2023) and the ACM Code of Ethics (ACM, 2023) to ensure ethical responsibility in both design and development. Key ethical concerns include fair competition, safety of participants and bystanders, and transparency in development.

1> Fair Competition: We will ensure compliance with competition rules, avoiding unauthorized modifications that may provide an unfair advantage. All components used will comply with the competition’s technical regulations, and no deceptive practices will be employed.

2> Safety of Participants and Bystanders: The Battlebot will be tested in a controlled environment, ensuring it does not pose accidental risks to participants or observers.
3> Transparency in Development: We will maintain proper documentation of hardware and software to ensure integrity and reproducibility. Design files and testing reports will be kept up to date for reporting purposes.

Safety Concerns and Strategies
To ensure the safety of developers, users, and bystanders, we will implement the following safety measures in accordance with Occupational Safety and Health Administration (OSHA, 2023) regulations.

Electrical Safety
Our project involves a 11.1V LiPo battery and high-torque motors, necessitating robust safety measures to prevent electrical hazards:

1> Battery Protection: The LiPo battery will be housed in an impact-resistant, ventilated enclosure to prevent overheating and mechanical damage.
2> Circuit Safety: Wires and power components will be properly insulated and undergo continuity and resistance testing to prevent short circuits or electrical failures (NFPA, 2023).
3> Emergency Shutoff: A physical kill switch will be integrated into the circuit, allowing for immediate power cutoff if an electrical failure occurs.

Mechanical Safety
The weapon system and chassis structure will be designed to minimize risk to operators and audience:

1> Finite Element Analysis (FEA): The chassis and weapon system will undergo stress and impact simulations to ensure they can withstand combat forces without unexpected failure.
2> Material Safety: The bot will be 3D-printed with PLA+ plastic, selected for impact resistance and durability.

Pneumatic Safety
Pressure Limits Compliance
- Do not exceed 120 PSI during normal operation.
- Safety buffer limit: 130 PSI maximum before automatic pressure release is triggered.

Pre-Operation System Check

- Inspect all air hoses, connections, and fittings for leaks or damage before every use.
- Check pressure gauge readings to ensure the system is within the safe operating range.
- Ensure the manual safety vent valve is functional before charging the system.

Safe Charging & Pressure Release

- Always charge the system in a well-ventilated area.
- Use only approved pressure sources with a regulator to prevent over-pressurization.
- Before maintenance, fully depressurize the system using the manual release valve.

Lab Safety Compliance
Development and testing will follow University of Illinois Lab Safety Guidelines, including:

1> Personal Protective Equipment (PPE): Team members will wear safety goggles, gloves, and anti-static wristbands when handling batteries, electrical circuits, and pneumatics.
2> Safe Work Practices: All testing will occur in designated safety zones, with emergency response plans in place.

Required Documentation

Given the high-risk factors associated with pneumatics, high voltage, and combat interactions, we will develop a comprehensive Safety Manual that includes:

- Emergency Procedures: Clear steps to handle system failures, air leaks, electrical shorts, and unintended solenoid activation.
- Risk Mitigation Strategies: Guidelines for safe handling of pressurized air systems, battery management, and ESD protection for electronic components.
- Safe Handling Guidelines: Standard operating procedures (SOPs) for system assembly, maintenance, and combat deployment.

Demonstration of Safety Compliance

- Adherence to Best Practices: During the final demo, we will showcase strict compliance with our Safety Manual, demonstrating that all team members follow safety protocols.
- Pneumatic System Integrity Test: Before operation, we will verify that all connections hold pressure without leaks, ensuring the gas tank, solenoid, and actuator function correctly.
- Electrical Safety Measures: We will implement proper insulation, fuse protection, and emergency cutoff switches to prevent accidental system overloads.
●

# References

IEEE. "IEEE Code of Ethics." 2023. https://www.ieee.org/about/corporate/governance/p7-8.html ACM. "ACM Code of Ethics and Professional Conduct." 2023. https://www.acm.org/code-of-ethics OSHA. "Occupational Safety and Health Administration Regulations." 2023. https://www.osha.gov/NFPA. "National Fire Protection Association Electrical Safety Standards." 2023. https://www.nfpa.org/

University of Illinois. "Division of Research Safety." 2023. https://www.drs.illinois.edu/

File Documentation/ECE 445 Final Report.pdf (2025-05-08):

# Ant-weight, 3D Printed Battlebot

By
Justin Leong(jyleong2)
Yuxuan Nan(yuxuann2)
Zilong Jiang(zjian4)

Final Report for ECE 445, Senior Design, Spring 2025 TA: Bill Yang

07 December 2025
Project No. 1

## Abstract

This report describes the process of designing, building, and testing a 3D-printed Battlebot for the Ant-weight class of robotic combat with specific guidelines and requirements. The goal and what we ultimately created was a lightweight, durable robot capable of performing quick and precise movements while delivering powerful attacks using a pneumatic flipping mechanism. Our 3D-printed Battlebot was developed utilizing an ESP32 microcontroller, contains a pneumatic scooping weapon, and moves on two “sticky” wheels powered by high torque motors, all wirelessly controlled by our controller app on our phones. After extensive testing, the robot met all key performance goals, including responsive control, reliable flipping power, structural durability, and enough battery life to last through a full match.

ii

## Contents

iii

## 1. Introduction

Robotic combat presents a unique challenge at the intersection of mechanical design, embedded systems, and power management. In our case, we wanted to take part in the Ant-weight 3D printed Battlebot division competition that would be hosted by Professor Gruev at the end of the Spring 2025 semester. For our case, the problems include the Ant-weight division limiting the robots’ weights to approximately two pounds. As such, this demands trade-offs between durability, agility, and weight. Furthermore, the Battlebot must also meet requirements of having enough battery power and the correct battery type to move quickly and use its weapon effectively. Finally, the Battlebot must also be able to be controlled wirelessly while also following certain structure material guidelines.

This project addresses those challenges through the design and construction of a 3D-printed Battlebot equipped with a pneumatic flipping weapon and wireless control via Bluetooth. Beyond mechanical and electrical design, the project also required thoughtful consideration of system integration, power regulation, and verification through testing. A 11.1V LiPo battery supplies power to all subsystems, while a buck converter steps down voltage for logic-level electronics. Each design decision was evaluated based on its contribution to performance, safety, and compliance with Ant-weight class rules.

Our goal and solution was to create a Battlebot that could hold its own in the final Ant-weight Battlebot competition. We wanted to ensure that it could take hits, move with agility, and react to commands instantly. To make that happen, we built a custom chassis utilizing PLA+ plastic. This material has the strength we need without exceeding our weight requirement for the chassis. Additionally, the Battlebot was powered by two high-torque motors, which would allow the Battlebot to drive and turn smoothly during matches. Furthermore, these motors also allowed for better offense capabilities. In terms of offensive capabilities, a pneumatic flipping mechanism was mounted that could reliably destabilize opponents. To control the entire system, the whole system is centered around the ESP32-WROOM-32E, which receives Bluetooth signals from the user and translates them into quick, responsive actions.

Ultimately, this report outlines our design and implementation process, and also provides the results of our Battlebot’s performance based upon the details of each subsystem. Our report also discusses technical challenges we encountered, how we developed solutions to counteract them, and future improvements that could enhance performance in a competitive setting.

### 1.1 Top Level Block Diagram (Original)


Figure 1. The original block diagram for our battlebot. This was the block diagram mostly followed in our design. However, it should be noted that in the power system, we never used a step down regulator and we also used a different buck converter. Furthermore, for our drivetrain, we ended up using a different H-Bridge chip due to complications in our circuit.

For the most part, this was the block diagram used in the creation for our final design. However, there were a few changes we had to make for the final design. Similar to what Figure 1 states, we never used a step down regulator in the power system. We had also used different chips for both the buck converter and H-Bridge (drivetrain). The H-Bridge change in chip was due to incorrectly wiring the circuit, which will be talked about in Section 2.2 Drivetrain. Additionally, it should be noted that we utilized a phone as our control device instead of a PC.

To be specific in what our top level block diagram contains, it contains the four subsystems of drivetrain, weapon and chassis, power, and control subsystems. The control system is the heart of our robot, giving signals to the rest of the Battlebot on what actions the user is inputting through a remote control via phone app. The signals may be sent to the weapon and chassis subsystem or the drivetrain subsystem. For the weapon and chassis subsystem, it will receive a single signal using GPIO from the microcontroller on when to activate and deactivate the weapon controlled via solenoid, the weapon being a pneumatic piston connected to a scooper. The other GPIO signal sent out from the microcontroller controls the drivetrain. The drivetrain receives a total of four signals that assist with controlling the motors through an H-Bridge module. Finally, the entire Battlebot is powered by our power subsystem. This power subsystem utilizes a 11.1V LiPo battery and a buck converter to output a 3.3V signal. The 11.1V signal is used to power the motor subsystem and trigger our solenoid. The 3.3V signal is used to power our ESP32 which can then send its own 3.3V signals to the drivetrain subsystem and the weapon and chassis subsystem.

## 2. Design

Our Battlebot was designed around four core subsystems: the drivetrain, weapon and chassis, power, and control subsystems. Each of these subsystems played a critical role in ensuring the Battlebot is fast, durable, and capable of delivering solid offensive strikes. Throughout the design process, we balanced performance, weight, and reliability by choosing components that were both effective and efficient.

### 2.1 Drivetrain

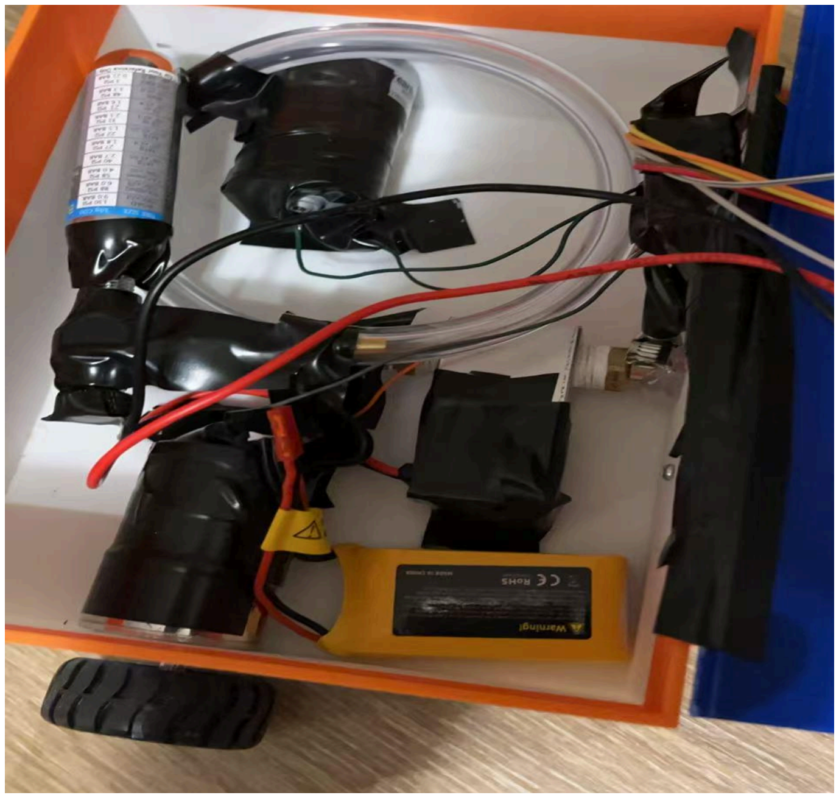
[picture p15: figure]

Figure 2. This is a picture of how our actual Battlebot was laid out. There are two motors towards the backside of the internal layout of our Battlebot. To control these two motors, we mounted our H-Bridge on the front wall of our Battlebot. The reasoning of using a different H-Bridge will be discussed later in Section 2.1 Drivetrain.

The drivetrain of our system served as the main component of how the Battlebot was able to move and maneuver around opponents. For choice of motors, the Greartisan high-torque DC motors propelled our Battlebot. Each of these motors provided roughly 2.2 kg⋅cm of torque, with a no-load speed of 200 RPM. Our motors could displace enemies up to 4.4kg (1)(2) under ideal conditions where coefficient of friction is 1 with both motors. These were seated at the back of our robot to ensure that our front scooper was as close to the ground as possible at a steeper angle, which can be seen in Figure 2. Additionally, we utilized “sticky” tires that would best compliment these high torque motors. Tires with a maximum amount of grip would allow our robot to utilize the maximum amount of torque and be able to drive well in the arena without slipping. In our original design, we wanted to put omni-directional balls at the front or an omni-directional wheel, but due to the height increase this would elevate our Battlebot by, we decided against implementing this in our final design. Instead, we wanted our scooper to be close to the ground, thus removing these front omni-wheels or omni-ball would best compliment the weapon.

Ftorque = torque / radius = (2.2 kg*cm * 9.81 N*m / kg*cm) / 0.01m = 21.582N (1) Total Weight Displaceable = Ftorque / (μk

* g) = 21.582N / (1 * 9.81) = 2.2 kg (2)


Figure 3. This is a schematic of how we wired our original drivetrain subsystem. The drivetrain subsystem is centered around the DRV8833RTY chip from Texas Instruments.

Based on Figure 3, the schematic of how the drivetrain’s H-Bridge was wired in the PCB is demonstrated. In this original layout from the PCB, it should be noted that an incorrect wiring was made. Due to how the DRV8833RTY chip should inherently be wired, the VM pin was incorrectly given access to the 12V rail from the battery. This is an issue that essentially shorted or fried the H-Bridge chips we had on hand for this specific module due to the fact that the max voltage the VM pin is able to handle is 10.8V [7]. We were able to detect this issue by checking the nFault pin which would display an output logic level zero if the chip has incurred a fault condition. The fault conditions that we had deduced this to were either burning or over-volting to the chip.

To solve the issue of having fried our DRV8833RTY H-Bridge modules, we decided to use an external H-Bridge module – the L9110s DC motor driver module. This new H-Bridge module functioned similar to our original module, with it accepting four inputs to directionally control the outputs. The H-Bridge logic of the DRV8833RTY and L9110s H-Bridge modules can be seen in Table 1. However, this new L9110s H-Bridge module, on the other hand, accepted up to a maximum of 12V without short circuiting in comparison to the maximum 10.8V the
DRV8833RTY can handle.

Table 1. H-Bridge Logic

xIN1 | xIN2 | xOUT1 | xOUT2 | Function
0 | 0 | Z | Z | Coast/fast decay
0 | 1 | L | H | Reverse
1 | 0 | H | L | Forward
1 | 1 | L | L | Brake/slow decay

### 2.2 Weapon and Chassis

The primary weapon we designed is a Pneumatic Ramp Flipper, specifically designed to flip or destabilize opponents with precision and efficiency. It features a low-profile, angled ramp that smoothly slides underneath for effective lifting. The system originally was designed to operate using a pneumatic actuator connected to a 200ml gas tank pressurized at 120 PSI, enabling controlled solenoid valve activation for each flip. However, we had actually opted to buy CO2 cartridges that held above the pressurized 120 PSI, which were more cost effective and easier to source. This also made our design more easily swappable between fights instead of having to find a location to refill our cartridges.

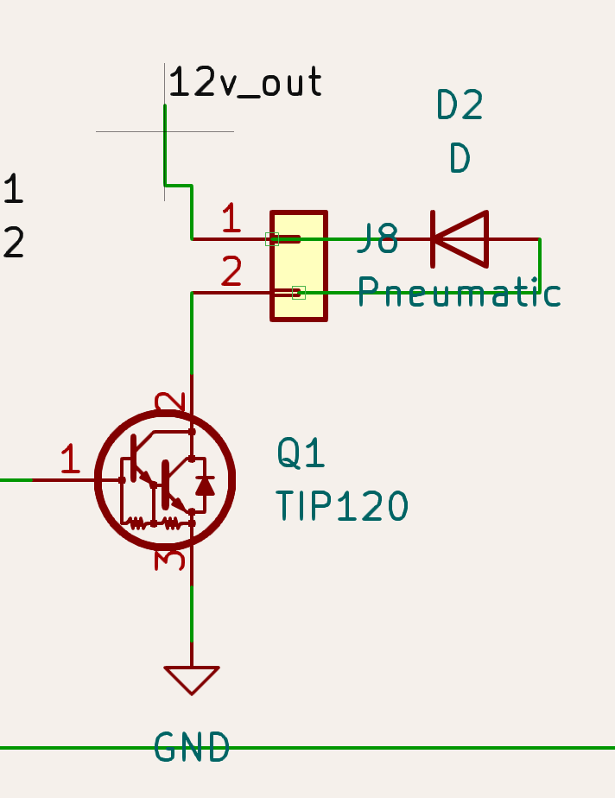
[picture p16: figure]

Figure 4. The actual schematic of our Pneumatic system and how it would be activated. The signal for the transistor comes from our control system through a 10kΩ resistor.

Originally, we had wanted to activate our weapon system utilizing a NMOS transistor, however, the voltage outputted by our ESP32 would not consistently meet the requirement of 3.3V-3.6V to trigger and close the gate. As such, we had to transition to a BJT gate which would be controlled by current. This way, there would be no reliance on our ESP32 to output above 3.3V consistently as we were only able to get a consistent output of 3.25V. Additionally, this meant the solenoid could also be reliably opened and closed utilizing the BJT transistor. Furthermore, this new portion of the circuit was wired the way it was to have a 12V to trigger the solenoid as well as have a flyback diode to give the inductive load spike a safe path to circulate. Finally, we also wired a 10kΩ resistor between the BJT and the microcontroller to minimize current draw from the microcontroller.

In terms of chassis, we still continued with using PLA+ plastic for our 3D prints. This is because of PLA+’s offering a balance between durability and weight efficiency. Furthermore, it is also less brittle in comparison to PLA, meaning an increased impact resistance. Finally, for our final design, we had opted to mount heavy components at the bottom of the chassis to lower the center of gravity (refer to Figure 2). Additionally, we had opted for two layers of a ramp and scooper to be able to more easily scoop under opponents.

### 2.3 Power System

Our Battlebot is powered by a 3-cell (3S) 11.1V LiPo battery rated at 500mAh. We had selected the LiPo variant battery as this was one of the provided battery types safe to use in the Antweight Battlebot competition. Additionally, while the battery was labeled as 11.1V, we could charge it to voltages around 11.8V or even 12V at full charge. This provides a strong and consistent power source for both the motors and the pneumatic weapon system, which are wired directly to the battery and operate comfortably within that voltage range. However, the ESP32 microcontroller requires a much lower operating voltage – specifically 3.3V. To supply the ESP32 safely, we used an LM2596S-3.3 buck converter to step down the battery voltage. This converter takes the ~12V input from the battery and reliably outputs 3.3V to power the logic side of our control system. Without this step-down circuit, the ESP32 would be damaged due to overvoltage as it has a max voltage of 3.6V [6].

By splitting our power delivery this way—sending the full battery voltage to high-power components like the motors and solenoid, while using the buck converter for the ESP32 – we were able to simplify our wiring and avoid unnecessary regulators or converters for the rest of the system. We tested the battery under full load and confirmed that it could consistently power all components for more than 2 minutes, which exceeds the length of a typical match and meets the project’s performance goals. In actuality, the battery could last up to ~10 minutes under specific conditions and loads.

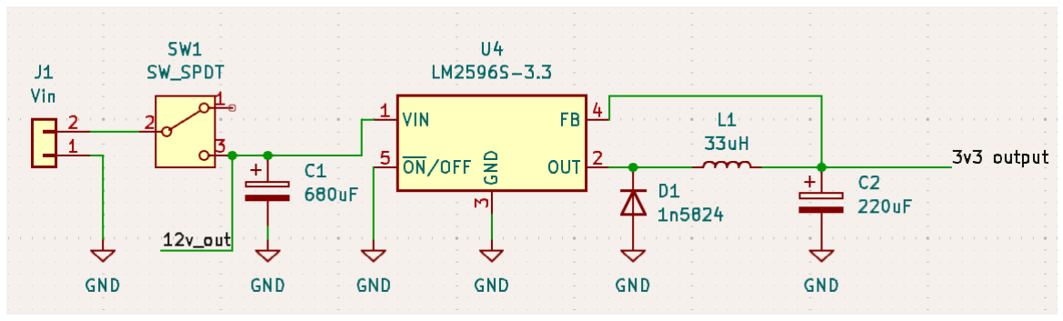
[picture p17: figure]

Figure 5. A schematic of our power subsystem and what it would output. There are two points of shutoff to ensure our system has a safe shutoff – the switch and connector to battery.

This buck converter circuit steps down a 12V input to 3.3V for powering low-voltage components like the ESP32. The capacitors help smooth voltage fluctuations – C1 at the input and C2 at the output – while the inductor and diode ensure efficient energy transfer during switching. The diode also provides a return path for current when the switch is off, preventing voltage spikes and improving overall circuit stability and efficiency.

It should be noted that contradictory to our original block diagram in Figure 1, we do not use a step down regulator. This is because our buck converter – LM2596S-3.3 – safely steps down our voltage from 12V to 3.3V safely without too much heat, removing the need for a step down regulator.

2.3.1 Tolerance Analysis
In our original tolerance analysis, we calculated the type of battery required based upon the factor that competition rounds were approximately two minutes long.

The motor we selected (at 12V) has a max efficiency of 0.1A draw with a 2A stall current.

Average and Peak Current Draw of both motors:
Imotors = Nmotors * Imotor = 2 * 0.1A = 0.2A | (3)
IpeakM = Nmotors * Imotor_peak = 2 * 2A = 4A | (4)

Our Pneumatic system has a rough average current draw of 3A with a peak current draw of 5A. Additionally, our ESP32 and related components have an average current draw of 0.15A and a peak current draw of 0.2A.

The calculation of how much our battery capacity need as well as tolerance can be calculated as follows:

Total and Peak Current Draws:
Itotal = Imotors + Ipneumatic + IIC = 0.2A + 3A + 0.15A = 3.35A | (5)
Ipeak = Imotors_peak + Ipneumatic_peak + IIC_peak = 4A + 5A + 0.2A = 9.2A | (6)
Capacity of Battery Wanted = Itotal

* Total Time = 3.35A * 2min = 3.35 * 2/60 h = 0.1116 Ah (7)
Peak current of battery = 9.2A | (8)
3.35A/500mAh = 6.7C | (9)
9.2A/500mAh = 18.4C | (10)

Because actual consumptions with batteries will vary, we need to make sure that the battery can handle 9.2A of peak load draw as well as have a total capacity of at least 0.1116Ah (7). This will ensure that the battery can handle the components we are using as well as last the total battlebot round of 2 minutes. The battery we have opted for has a capacity of 500mAh - which satisfies the capacity of battery wanted by a lot to ensure even with not optimal conditions it will work -as well as discharge rate of 35C and max discharge rate of 70C. To ensure that the peak current and current ratings are within this discharge rate, we take the amperage divided by the total capacity of the battery (9)(10), both of which are within limits: 6.7C < 35C and 18.4C < 70C.

While these calculations were all estimations, they were pretty close to our actual draws and thus satisfied our requirements. It should be noted that with both motors running, there is approximately 0.3A of current draw with a peak of 1A. The pneumatic system also draws approximately 0.5A of current for triggering, meaning that the minimum and maximum peaks of current draw range between 0.3A and 1.5A.

### 2.4 Control System

To serve as our central processing unit, the ESP32-WROOM-32E served as our microcontroller. This ESP32 offers both WiFi and Bluetooth, perfect for our design to wirelessly control our Battlebot while also having enough pins for the Drivetrain and Weapon/Chassis subsystems. Originally, our design opted to utilize a PC as our main controller. However, we found this very “clunky” in a sense and opted to wirelessly control it from our phones. Additionally, we had swapped from Bluetooth, to WiFi (using hotspot), back to Bluetooth. This was due to the fact that we originally thought that Bluetooth would have too much input delay, however, this was not the case. The reason why we swapped from WiFi back to Bluetooth as well is the fact that WiFi utilizing a hotspot introduces more room for error. There would be more points of failure, that being the hotspot we would need to connect to, as well as both our Battlebot and PC controller needing to connect to that. As such, we had decided to transition back to Bluetooth, which offers individual private connections as well as fast response times, under 100ms, for low-latency executions.

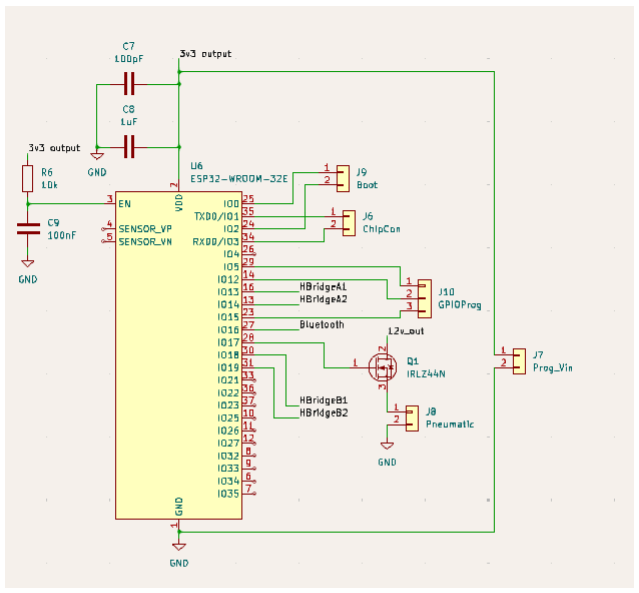
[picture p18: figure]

Figure 6. Our schematic for the control subsystem. It should be noted that the weapon subsystem is included but is also outdated, more can be found in the section 2.2 Weapon and Chassis.

Once again from Figure 6, it should be noted that the weapon subsystem portion of this schematic is incorrect, and an updated version can be found in the previous Weapon and Chassis subsystem. While there aren’t many deviations from this design for our microcontroller schematic, it should be noted that to actually wire our new drivetrain, we had directly connected wires to the pins labelled with “HBridge”. This was because the layout for the DRV8833RTY was actually too small for connections.

Finally, in terms of code, we had utilized an Arduino library that we modified for our purpose. That library is called “Dabble”, as it provides a phone app with a controller, perfect for our Battlebot use case. This library was able to send signals to our microcontroller to control the directions as well as have buttons for triggering our pneumatic system. Furthermore, we were able to connect LEDs to show that we had powered up and had Bluetooth connections enabled for our system. Additionally, when wirelessly controlling our Battlebot, the connection timings when inputting our controls were all 100ms or less – with an average of ~90-100ms during one of our test sessions (utilizing a timer) – meaning that the testing had been verified for low latency connection.

## 3. Design Verification

Table 2. Drivetrain Requirements and Verification
Requirements | Verification
Can produce a maximum of 2.2kg*cm of torque under no load | ● Tested by pushing something of 2.2kg for approx. 1cm ● Ended up using the battlebot to push roughly 4lbs (close to 2.2kg) for over 1 meter with our final battlebot
Can reach a maximum of 210 rpm under no load | ● We did not have a tachometer, counted revolutions of a spinning tape and approximated/calculated the rpm ● Roughly 210 rpm (3.5 revolutions per second)

Table 3. Weapon and Chassis Requirements and Verification
Requirements | Verification
1.5A battery current draw requirement | ● Measured current draw of solenoid trigger at 0.5A
Solid build structure using PLA+ plastic - Able to move and withstand ramming 2 lbs | ● Our robot can move/push over 4 lbs of weight (ramming robot into the 4lbs)
Gas tank that can withhold 120 psi for pneumatic weapon | ● We utilized pre-filled CO2 cartridge that holds over 120psi; tube was approximately 8in long, ¼ in diameter ● Able to launch over 7 fully power flips

Table 4. Power Subsystem Requirements and Verification
Requirements | Verification
Can supply continuous 3A of current to all subsystems when underload | ● Measured current, varied from 0.3A to 1.5A when all subsystems are underload, meaning our design works very efficiently compared to planned maximum current
Has enough capacity to last 2 minutes of continuous usage | ● Our full design under load lasts longer than 2 minutes ● Ran a timer, roughly ~10 minutes under load

Table 5. Power Subsystem Requirements and Verification
Requirements | Verification
Connect via Bluetooth | ● Able to use phone (Dabble library) to connect to Battlebot; ~100ms signal transmission times (timer) ● LED to display bluetooth is in use
Be able to control all 4 directional movements of battlebot with given signals -left, right, forward, backwards | ● Able to move in the 4 directions properly using the directional movements ● H Bridge A1,A2,B1,B2

## 4. Costs and Schedule

### 4.1 Parts

Table 6. Final Design Parts Costs

Part | Manufacturer | Retail Cost ($) | Bulk Purchase Cost ($) | Actual Cost ($)
PLA+ Filament | Amazon | $16.99 | $16.99 | $16.99
DC 12V 200RPM Gear Motor | Amazon | $14.99 | $29.98 | $29.98
RCBattery | rcbattery.com | $10.99 | $10.99 | $10.99
220uf capacitor | Mouser Electronics | $1.19 | $1.19 | $1.19
680uf capacitor | Mouser Electronics | $1.08 | $1.08 | $1.08
diodes | ebay | $2.21 | $2.21 | $2.21
10mH inductor | Switch Electronics | $2.03 | $4.06 | $4.06
33uH inductor | Digi-Key Corporation | $0.18 | $0.54 | $0.54
solenoid valve | Amazon | $9.65 | $9.65 | $9.65
single return cylinder | Amazon | $18.28 | $18.28 | $18.28
co2 gas | Amazon | $23.90 | $23.90 | $23.90
gas hose | Amazon | $14.69 | $14.69 | $14.69
buck converter | Digi-Key Corporation | $7.89 | $23.67 | $23.67
H bridge | Digi-Key Corporation | $1.87 | $5.61 | $5.61
Esp32 | Digi-Key Corporation | $4.36 | $13.08 | $13.08
switch | Digi-Key Corporation | $2.68 | $2.68 | $2.68
wheels | ebay | $2.59 | $2.59 | $2.59
Total | | | | 181.18

It should be noted that some parts were bought ourselves, but were factored into the total costs.

### 4.2 Labor

The total labor cost is calculated as $40 × 60 = $2,400.
For the EE student and $38 × 60 = $2,280 per CE student,
resulting in a total labor cost of 2*$2280+$2400= $6,960 for the team.

### 4.3 Schedule

Table 7. Schedule
Week (date) | Group Members | Tasks
3/3 | Justin, Yuxuan | Able to send signal by using esp32 through wifi
3/10 | Zilong, Justin | Finish the pcb design
3/24 | Zilong | Figure out how to use the correct mosfet for our design
3/31 | Zilong, Justin, Yuxuan | Fix the pcb design and order in the third round.
4/7 | Zilong, Justin, Yuxuan | We keep soldering the pcb board, and test the pneumatic weapon in breadboard
4/14 | Zilong, Justin, Yuxuan | Keep testing pcb board and resoldering another PCB board
4/21 | Zilong, Justin, Yuxuan | Combine all the designs together and print the chassis

## 5. Safety and Ethical Considerations

5.1 Ethical Considerations
Our project adheres to the IEEE Code of Ethics [1] and the ACM Code of Ethics [2] to ensure ethical responsibility in both design and development. Key ethical concerns include fair competition, safety of participants and bystanders, and transparency in development.
1. Fair Competition: We will ensure compliance with competition rules, avoiding unauthorized modifications that may provide an unfair advantage. All components used will comply with the competition’s technical regulations, and no deceptive practices will be employed.
2. Safety of Participants and Bystanders: The Battlebot will be tested in a controlled environment, ensuring it does not pose accidental risks to participants or observers.
3. Transparency in Development: We will maintain proper documentation of hardware and software to ensure integrity and reproducibility. Design files and testing reports will be kept up to date for reporting purposes.

5.2 Safety Concerns and Strategies
To ensure the safety of developers, users, and bystanders, we will implement the following safety measures in accordance with Occupational Safety and Health Administration [3] regulations.

5.2.1 Electrical Safety
Our project involves a 11.1V LiPo battery and high-torque motors, necessitating robust safety measures to prevent electrical hazards:

To reduce the risk of short circuits, we took several practical steps during both assembly and testing. One specific measure involved taping over any exposed metal parts, such as screw heads or frame components, that were close to the PCB. This prevented accidental contact between conductive surfaces and the circuit board, which could otherwise result in a short. In addition, we used heat-shrink tubing on all soldered wires, properly insulated power lines, and organized cables to avoid tangling or friction. We also performed continuity checks before powering the system to ensure that no unexpected connections were present.

5.2.2 Mechanical Safety
The weapon system and chassis structure will be designed to minimize risk to operators and audience:
- Finite Element Analysis (FEA): The chassis and weapon system will undergo stress and impact simulations to ensure they can withstand combat forces without unexpected failure.
- Material Safety: The bot will be 3D-printed with PLA+ plastic, selected for impact resistance and durability.

5.2.3 Pneumatic Safety
Pressure Limits Compliance
- Do not exceed 120 PSI during normal operation.
- Safety buffer limit: 140 PSI maximum before automatic pressure release is triggered. Pre-Operation System Check
- Inspect all air hoses, connections, and fittings for leaks or damage before every use.

Safe Charging & Pressure Release
- Always charge the system in a well-ventilated area.
- Use only approved pressure sources with a regulator to prevent over-pressurization.
- Before maintenance, fully depressurize the system using the manual release valve.

5.3 Lab Safety Compliance
Development and testing will follow University of Illinois Lab Safety Guidelines, including:
1. Personal Protective Equipment (PPE): Team members will wear safety goggles, gloves, and anti-static wristbands when handling batteries, electrical circuits, and pneumatics.
2. Safe Work Practices: All testing will occur in designated safety zones, with emergency response plans in place.

5.4 Required Documentation
Given the high-risk factors associated with pneumatics, high voltage, and combat interactions, we will develop a comprehensive Safety Manual that includes:
- Emergency Procedures: Clear steps to handle system failures, air leaks, electrical shorts, and unintended solenoid activation.
- Risk Mitigation Strategies: Guidelines for safe handling of pressurized air systems, battery management, and ESD protection for electronic components.
- Safe Handling Guidelines: Standard operating procedures (SOPs) for system assembly, maintenance, and combat deployment.

5.5 Demonstration of Safety Compliance
Adherence to Best Practices: During the final demo, we will showcase strict compliance with our Safety Manual, demonstrating that all team members follow safety protocols.
- Pneumatic System Integrity Test: Before operation, we will verify that all connections hold pressure without leaks, ensuring the gas tank, solenoid, and actuator function correctly.
- Electrical Safety Measures: We will implement proper insulation, fuse protection, and emergency cutoff switches to prevent accidental system overloads.

## 6. Conclusion

Over the course of the semester, we successfully designed, built, and tested a Bluetooth controlled 3D Printed Ant-weight Battlebot. The robot integrated a pneumatic flipping weapon, dual-motor drivetrain, custom PLA+ chassis, and reliable power and control systems. In our final tests, it met key performance goals: it was responsive to wireless commands, drove in the four directions required, activated its weapon, and was structurally durable during collisions. By precisely opening the cartridge, we confirmed that the weapon system did not leak any gas. During testing and competition, triggering the system allowed the piston to successfully flip the ramp at least 5 times without failure. The control interface worked reliably with under 100ms latency, and the power system remained stable during extended operation.

One area where the design did not fully meet competition requirements was weight. Our chosen motors provided excellent torque but were heavier than anticipated, causing the bot to slightly exceed the weight limit by approximately ~½ pounds over the Ant-weight classification. While the robot performed effectively in practice, this made it non-compliant for official competitive entry. This issue was identified during testing and verified by scale measurements, highlighting the trade-off between torque output and weight constraints. Another issue we would like to address was utilizing a separate H-Bridge module due to the incorrect wiring of the 12V to the max voltage of 10.8V input on our original H-Bridge module which inevitably sent through our measured 11.1V+ battery voltage to the H-Bridge VM pin which can only accept the max 10.8V. This can be fixed in the future by finding either a compatible H-Bridge module with our specifications, or having a way to step down the voltage to below 10.8V.

In future iterations, we plan to address the weight issue by selecting more compact and lightweight motors that still provide adequate torque. There are numerous lighter motors on the market that we could utilize and still be able to accomplish our goals, meaning that there can be further improvements to optimizing the weight of the motors while also maintaining a high amount of torque and speed. We also see potential for optimizing the chassis geometry further, possibly reducing material usage while maintaining structural integrity. Having a more sleekly designed chassis will ensure our Battlebot cannot be flipped from behind like what occurred in round 2 of the competition. Furthermore, our wheels on our chassis were placed quite high, making it really easy to slide a scooping mechanism underneath our chassis. Changing this in the future will also ensure that the Battlebot will not be as easily flipped from behind.

## References

[1] IEEE, "IEEE Code of Ethics," 2023. https://www.ieee.org/about/corporate/governance/p7-8.html
[2] ACM, "ACM Code of Ethics and Professional Conduct," 2023. https://www.acm.org/code-of-ethics
[3] OSHA, "Occupational Safety and Health Administration Regulations," 2023.https://www.osha.gov/
[4] NFPA, "National Fire Protection Association Electrical Safety Standards," 2023. https://www.nfpa.org/
[5] University of Illinois, "Division of Research Safety," 2023. https://www.drs.illinois.edu/
[6] Espressif Systems, "ESP32-WROOM-32E/ESP32-WROOM-32UE Datasheet," version 1.3, Jan. 20, 2023.
https://www.espressif.com/sites/default/files/documentation/esp32-wroom-32e_esp32-wroom-32ue_datasheet_en.pdf
[7] Texas Instruments, "DRV8833 Dual H-Bridge Motor Driver Datasheet," Nov. 2013. https://www.ti.com/lit/ds/symlink/drv8833.pdf

## Appendix A Requirement and Verification Table

Table 8. System Requirements and Verifications

Requirements | Verification | Verification Status (Y/N)
Drivetrain Requirements 1. Can produce a maximum of 2.2kg*cm of torque under no load 2. Can reach a maximum of 210 rpm under no load | Drivetrain Verifications 1. — a. Tested by pushing something of 2.2kg for approx. 1cm b. Ended up using the battlebot to push something of roughly 4lbs (close to 2.2kg) with our final battlebot 2. — a. We did not have a tachometer, counted revolutions and approximated the rpm b. Roughly 210 rpm (3.5 revolutions per second) | 1. Y 2. Y
Weapon and Chassis Requirements 1. 1.5A battery current draw requirement 2. Solid build structure using PLA+ plastic a. Able to move and withstand ramming 2 lbs 3. Gas tank that can withhold 120 psi for pneumatic weapon | Weapon and Chassis Verification 1. — a. Measured current draw with the solenoid trigger is 0.5A 2. — a. Our robot can move/push over 4 lbs of weight (ramming robot into the 4lbs) 3. — a. We utilized pre-filled CO2 cartridge that holds over 120psi; tube was approximately 8in long, ¼ in diameter b. Able to launch over 7 fully power flips | 1. Y 2. Y 3. Y
Power Requirements 1. Can supply continuous 3A of current to all subsystems when underload 2. Has enough capacity to last 2 minutes of continuous usage | Power Verification 1. — a. Measured currents, actual current amounts vary from 0.3A to 1.5A when all subsystems are underload, meaning our design works very efficiently compared to planned maximum current 2. — a. Our full design under load lasts longer than 2 minutes b. Ran a timer, roughly ~10 minutes under load | 1. Y 2. Y
Control Subsystem 1. Connect via Bluetooth | Control Verification 1. — | 1. Y 2. Y

2. Be able to control all 4 directional movements
of battlebot with given
signals - left, right,
forward, backwards
a. Able to use phone (Dabble library) to connect to Battlebot; ~100ms signal transmission times
b. LED to display bluetooth is in use
2. —
a. Able to move in the 4 directions properly pushing the directional buttons
b. H Bridge A1,A2,B1,B2

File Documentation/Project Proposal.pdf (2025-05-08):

# ECE 445 Spring 2025 Senior Design Project Proposal

# Project #1: Ant-weight, 3D Printed Battlebot

# Team Members: Yuxuan Nan(yuxuann2) Justin Leong (jyleong2) Zilong Jiang(zjian4)

# TA: Bill Yang Professor: Viktor Gruev

# 1. Introduction

## 1.1 Problem

The issue at hand is an Ant-weight, 3D Printed Battlebot Competition in which each team wants to win. There are certain constraints of the Battlebots’ design in order to be eligible and win. To win the competition, the goal of a battlebot is to outlast or destroy the opponent team’s battlebot. Different teams will have different designs, meaning a battlebot designed for winning must take into account as many factors to withstand and outlast the competition.

## 1.2 Solution

We decided upon developing a 3D Printed Bluetooth-controlled battle bot powered by an STM32 microcontroller. The Battlebot communicates with a PC via a Bluetooth module, enabling wireless command and control. It is equipped with two DC motors driven by H-bridge circuits for precise movement and a ramp-shaped weapon system for engaging in battles. The STM32 manages motor control using GPIO and PWM, while the weapon system utilizes GPIO or I2C protocols for activation. The bot integrates real-time communication, robust motor control, and weapon functionality, offering an engaging and functional design. My goal is to create a responsive and competitive robot for dynamic competitions.

## 1.3 Visual Aid

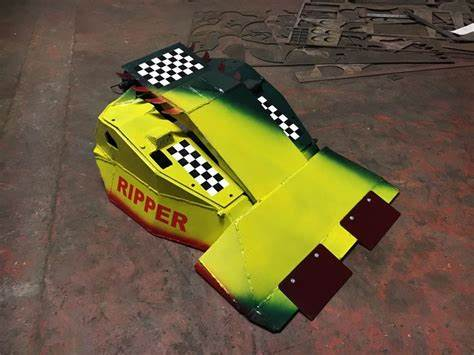
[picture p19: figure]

## 1.4 High-level requirements list

The Battlebot will be controlled wirelessly via Bluetooth with a response time of under 100ms.

- The drivetrain will consist of two high-torque DC motors powered by an H-bridge circuit, enabling precise movement and speed control.
- The weapon system will be a Skid Bucket mechanism controlled via a pneumatic actuator, capable of flipping or destabilizing 2 lb opponents.
- The chassis will be 3D-printed using PLA+ plastic, ensuring durability while maintaining a low center of gravity for stability.
- The power system will utilize a 3S 11.1V 500mAh LiPo battery with a 40C discharge rate (20A max continuous discharge) and 3C charge rate (1.5A max) (Flex Innovations, 2025). (https://www.flexinnovations.com/product/3s-500mah-25c-lipo-battery/) The system includes voltage regulation and short-circuit protection to ensure reliable performance throughout the match.

# 2. Solution

## 2.1 Block Diagram

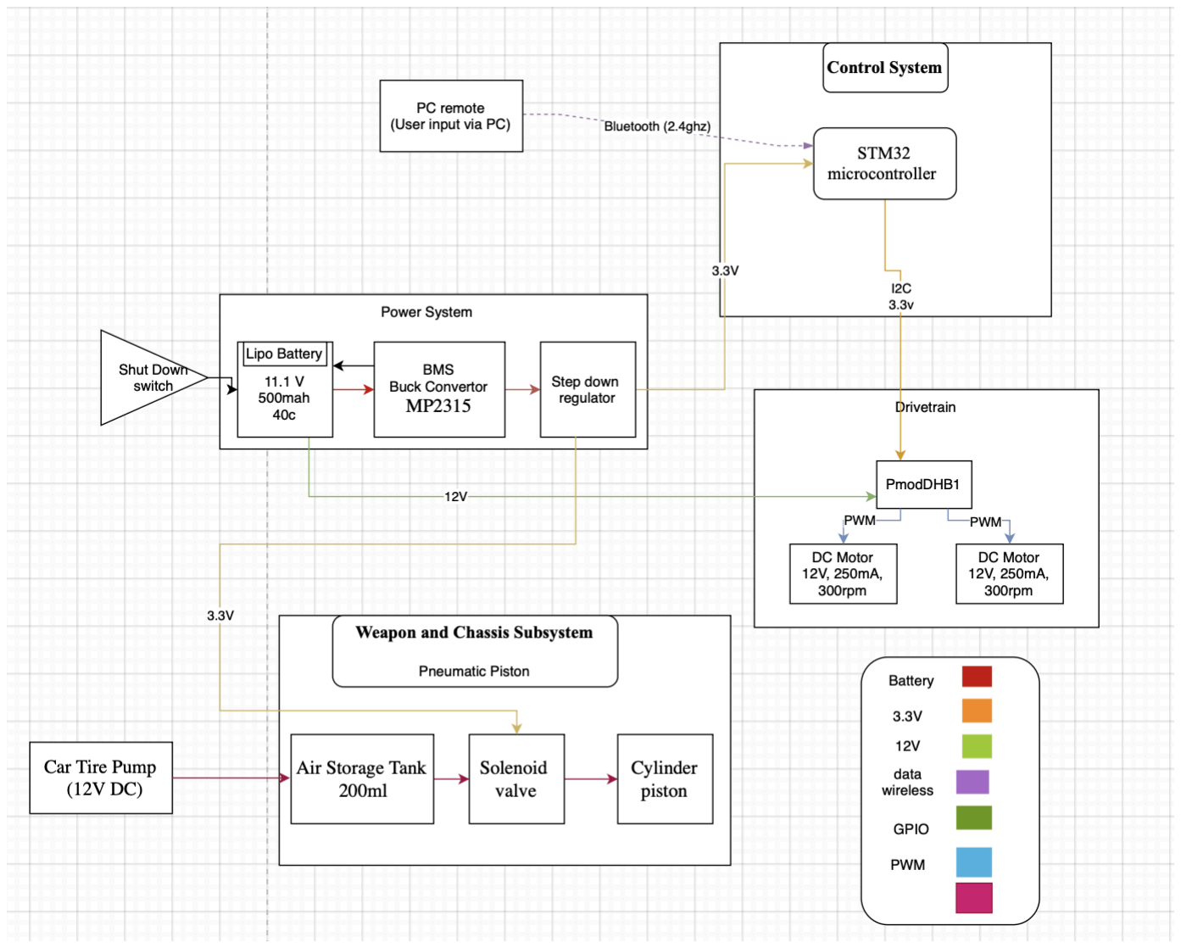
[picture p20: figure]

## 2.2 Subsystem Overview

Subsystem Analysis

1. Drivetrain Subsystem:

The drivetrain is responsible for the Battlebot’s movement and maneuverability. It utilizes two high-torque DC motors (Pololu 3204, 2025), (https://www.pololu.com/product/3204/specs) which provide 11 kg⋅cm of torque and a no-load speed of 300 RPM. These motors drive the rear wheels, enabling precise movement with enhanced torque for pushing against opponents. The motors are controlled via an H-bridge circuit, allowing bidirectional movement and speed control with improved efficiency. The circuit ensures the motors can dynamically adjust speed and direction for quick and strategic maneuvers. The battlebot employs PWM (Pulse Width

Modulation) signals from the STM32 microcontroller, ensuring variable speed control with smooth acceleration and deceleration.

The rear wheels are equipped with high-friction tires to maximize traction, enabling the bot to push against opponents effectively. The front wheel is omni-directional, ensuring smooth directional changes and enabling pivoting maneuvers. This combination optimizes the bot’s agility and defensive capabilities while maintaining stability during combat.

2. Weapon and Chassis Subsystem:

The primary weapon is a Skid Bucket system, designed for flipping opponents. The weapon operates through a pneumatic actuator that connects to a 200ml gas tank with 120 PSI, allowing controlled activation of the piston to flip the opponent. The system’s solenoid valve is controlled by the microcontroller for precise air release and timing. A pressure regulator ensures optimal pressure distribution, maintaining consistent flipping power while preventing excessive air consumption. Manual flow control valves allowing for safety release the pressured gas. The compact air tank is optimized to support up to 5 flips per charge.

The chassis is 3D-printed using PLA+ plastic, which offers a balance between durability and weight efficiency. PLA+ is selected over standard PLA due to its increased impact resistance and reduced brittleness. The chassis design features structural reinforcements in high-stress areas, ensuring it can withstand repeated impacts without compromising integrity.

The low center of gravity of the bot further improves stability, preventing easy flipping by opponents. Additionally, weight distribution is optimized to ensure consistent movement and controlled aggression during combat.

3. Power System Subsystem:

The power system ensures consistent and reliable power delivery to all components. A 3S 11.1V 500mAh LiPo battery (Flex Innovations, 2025) provides power to the drivetrain, control, and weapon subsystems.

The Pololu 3204 motors operate within a 6V-12V range, and since a fully charged 3S LiPo battery outputs 12.6V, the system can efficiently power the motors without additional voltage regulation. The battery voltage will naturally decrease during operation but will remain within the acceptable range.

A voltage monitoring circuit is integrated to track power levels and ensure the motors do not receive excessive voltage beyond their rated limits. The power system also includes overcurrent and short-circuit protection mechanisms, ensuring safety in case of electrical faults.

To supply lower voltage components such as the STM32 microcontroller and sensors, a step-down (buck) voltage regulator is used to convert the 11.1V battery output to stable 5V and 3.3V power. This ensures efficient and heat-minimized operation, preventing excessive power dissipation that would occur with a linear regulator. The regulated voltage allows stable operation of logic-level electronics while maintaining overall energy efficiency.

4. Control System Subsystem:

The STM32 microcontroller serves as the central processing unit of the Battlebot, handling real-time control inputs, motor operation, and weapon activation. The microcontroller is programmed to interpret Bluetooth commands from a PC controller, ensuring precise movement and attack execution.

The control system leverages PWM for speed modulation, GPIO for directional control, and I2C communication for sensor data (if applicable). The microcontroller processes commands with a response time of under 100ms, ensuring low-latency execution during battles.

The Bluetooth module is optimized for high-speed, interference-free communication, ensuring real-time command execution without signal drops. Extensive testing is conducted to mitigate latency issues and improve responsiveness.

## 2.3 Subsystem Requirements

Drivetrain Subsystem
- Each motor produce roughly 11kg * cm amount of torque (no load)
- Each motor can reach 300 RPM with no load, with load at least 160 RPM

Weapon and Chassis Subsystem
- Have a solid building structure of PLA+ plastic that can withstand the force of ramming 2lbs
- Have a gas tank that can withhold 120psi for the weapon

Power Subsystem
- Can supply a continuous 4.5A of current to all subsystems when under load (Check Tolerance Analysis)
- Have enough capacity to last 2 minutes of continuous usage to last the battle (our current battery is 500mAh)

Control System Subsystem
- Be able to connect via bluetooth from the computer we intend to use as a remote to our STM32 microcontroller and control/send signals to the different subsystems
- Be able to control the direction of the battlebot with given signals

## 2.4 Tolerance Analysis

An aspect of our design that may pose a threat to the successful completion is if our battery depletes before the end of the 2 minute time limit with the assumption that it is an endurance fight. In order to counteract this, we have decided to find a battery that will supply enough voltage to the different components while also having enough amperage such that it can sustain throughout the whole fight with extra power to spare.
To calculate the amount of amperage required of our battery, we need to calculate the power usage of all the subsystems based on a given time.

The motor we selected (at 12V) has a max efficiency of 0.82A draw with a 5A stall current.

Average and Peak Current Draw of both motors:
Imotors = Nmotors * Imotor = 2 * 0.82A = 1.64A

IpeakM = Nmotors * Imotor_peak = 2 * 5A = 10A

Our Pneumatic system has a rough average current draw of 3A with a peak current draw of 5A. Additionally, our STM32 and related components have an average current draw of 0.15A and a peak current draw of 0.2A.

The calculation of how much our battery capacity need as well as tolerance can be calculated as follows:

Total and Peak Current Draws:
Itotal = Imotors + Ipneumatic + IIC = 1.64A + 3A + 0.15A = 4.79A

Ipeak = Imotors_peak + Ipneumatic_peak + IIC_peak = 10A + 5A + 0.2A = 15.2A

Capacity of Battery Wanted = Itotal

* Total Time = 4.79A * 2min = 4.79 * 2/60 h = 0.1596 Ah Peak current of battery = 15.2A

Because actual consumptions with batteries will vary, we need to make sure that the battery can handle 15.2A of peak load draw as well as have a total capacity of at least 0.1596Ah. This will ensure that the battery can handle the components we are using as well as last the total battlebot round of 2 minutes. The battery we have opted for has a capacity of 500mAh - which satisfies the capacity of battery wanted by a lot to ensure even with not optimal conditions it will work - as well as discharge rate of 35C and max discharge rate of 70C. To ensure that the peak current and current ratings are within this discharge rate, we take the amperage divided by the total capacity of the battery (4.79A/500mAh = 9.58C and 15.2A/500mAh = 30.4C), both of which are within limits: 9.58C < 35C and 30.4C < 70C.

# 3. Ethics and Safety

Ethical Considerations:

Our project adheres to the IEEE Code of Ethics (IEEE, 2023) (https://www.ieee.org/about/corporate/governance/p7-8.html) and the ACM Code of Ethics(ACM, 2023), (https://www.acm.org/code-of-ethics) ensuring responsible design and ethical considerations throughout development. Ethical concerns specific to this project include: fair competition, Safety of Participants and Bystanders and Transparency in Development. We will ensure compliance with competition rules and avoid unauthorized modifications that provide an unfair advantage. Also, Adhering to Occupational Safety and Health Administration

(OSHA) regulations (OSHA, 2023) (https://www.osha.gov/) is crucial to preventing unintended harm during development and testing. This includes ensuring all team members wear appropriate personal protective equipment (PPE) such as safety goggles and gloves while handling electrical components, following lockout/tagout (LOTO) procedures to prevent accidental activation of the battlebot, and enforcing strict safety zones around active testing areas to protect bystanders from potential hazards. All hardware and software components will be documented to ensure project integrity and reproducibility.

Electrical Safety:

From IEEE safety guidelines and NFPA electrical safety standards (NFPA, 2023) (https://www.nfpa.org/) we know that wires and power components will be insulated and tested to prevent short circuits or electrical hazards.Wires and power components will be properly insulated and undergo continuity and resistance testing to detect any potential faults before deployment. The 11.1V LIPO battery will follow IEEE 1725-2011 battery management guidelines to prevent overheating and damage.The 11.1V LIPO battery battery will be housed in an impact-resistant, ventilated enclosure to prevent overheating and mechanical damage.

Mechanical Safety:

The battlebot’s chassis and weapon systems will undergo finite element analysis (FEA) to predict stress distribution and deformation under impact conditions.Simulated combat tests will be conducted to ensure structural integrity and resistance to high-force collisions.The battlebot’s weight distribution and center of gravity will be optimized to enhance stability and prevent tipping during combat.

The weapon actuation system will include redundant fail-safes to prevent unintended activation, ensuring safety during handling and maintenance.

Wireless Communication Reliability:

Since the bot relies on Bluetooth control, we will ensure low-latency response times and test for interference risks to avoid unintended loss of control.

Lab Safety Compliance:

Our development and testing will take place in University of Illinois laboratories, requiring strict adherence to campus safety policies. This includes compliance with University of Illinois Lab Safety Guidelines, OSHA electrical safety protocols, proper handling of PCB components, and adherence to lab-specific regulations to minimize hazards. Safety measures such as PPE usage, workspace organization, and risk assessments will be strictly followed to maintain a secure testing environment.

# 4. Reference

IEEE. "IEEE Code of Ethics." 2023. https://www.ieee.org/about/corporate/governance/p7-8.html

ACM. "ACM Code of Ethics and Professional Conduct." 2023. https://www.acm.org/code-of-ethics

OSHA. "Occupational Safety and Health Administration Regulations." 2023. https://www.osha.gov/

NFPA. "National Fire Protection Association Electrical Safety Standards." 2023. https://www.nfpa.org/

University of Illinois. "Division of Research Safety." 2023. https://www.drs.illinois.edu/

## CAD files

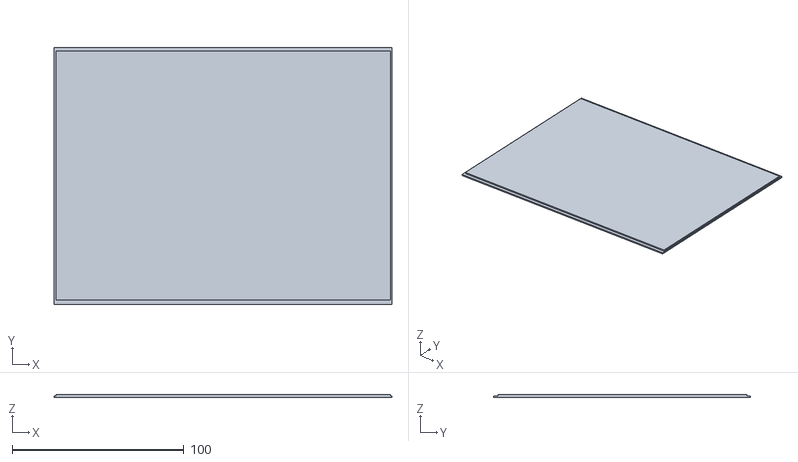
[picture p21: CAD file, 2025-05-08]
3D_Print/lid.stl
197.0 x 150.0 x 2.00

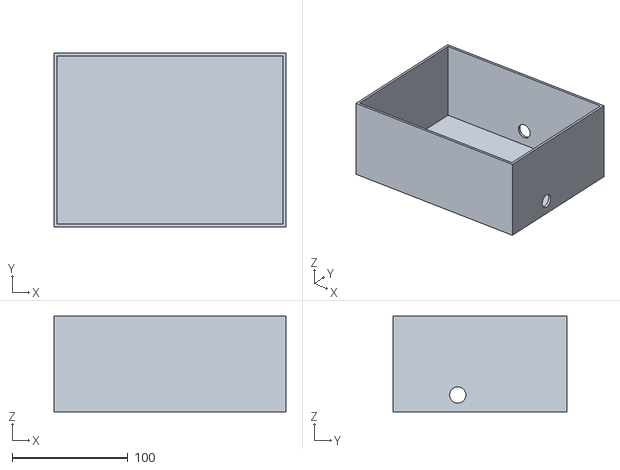
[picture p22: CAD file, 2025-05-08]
3D_Print/chasis.stl
200.0 x 150.0 x 82.5

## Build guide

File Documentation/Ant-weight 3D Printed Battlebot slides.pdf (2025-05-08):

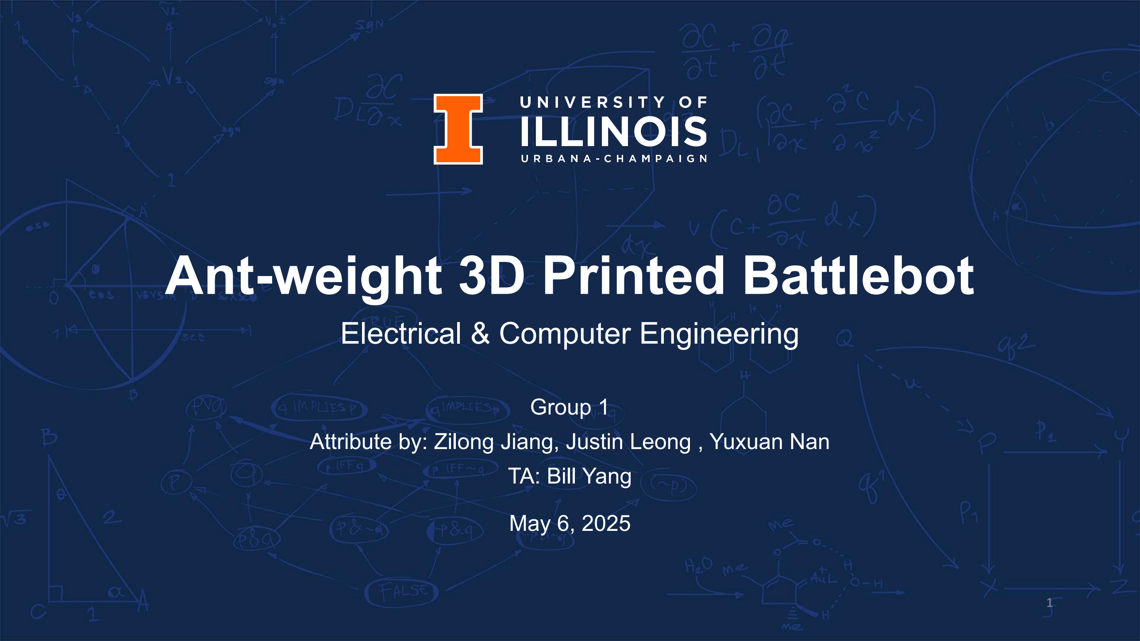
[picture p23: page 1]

# Ant-weight 3D Printed Battlebot

## Electrical & Computer Engineering

Group 1
Attribute by: Zilong Jiang, Justin Leong , Yuxuan Nan TA: Bill Yang

May 6, 2025

## What problem are we solving?

A competition for Antweight 3D Printed Battlebots was proposed. The problem is that everyone wants to win while also following all design constraints. The constraints included a weight limit of 2lbs, 3D printed structure, 2 minute rounds, etc. To win, our goal was to outlast/destroy differently designed Battlebots.

Factors to solve the problem!

- Designing an Ant-weight 3D-printed Battlebot for the Ant-weight Battlebot competition
- Combines PCB design, embedded systems, and wireless control
- Goal: Build a robot that is durable, responsive, and within weight limits
- Design a pneumatic weapon in order to scoop up competitors
- Focused on control, weapon function, and lightweight structure

## Introduction & Objective

ELECTRICAL & COMPUTER ENGINEERING | GRAINGER ENGINEERING

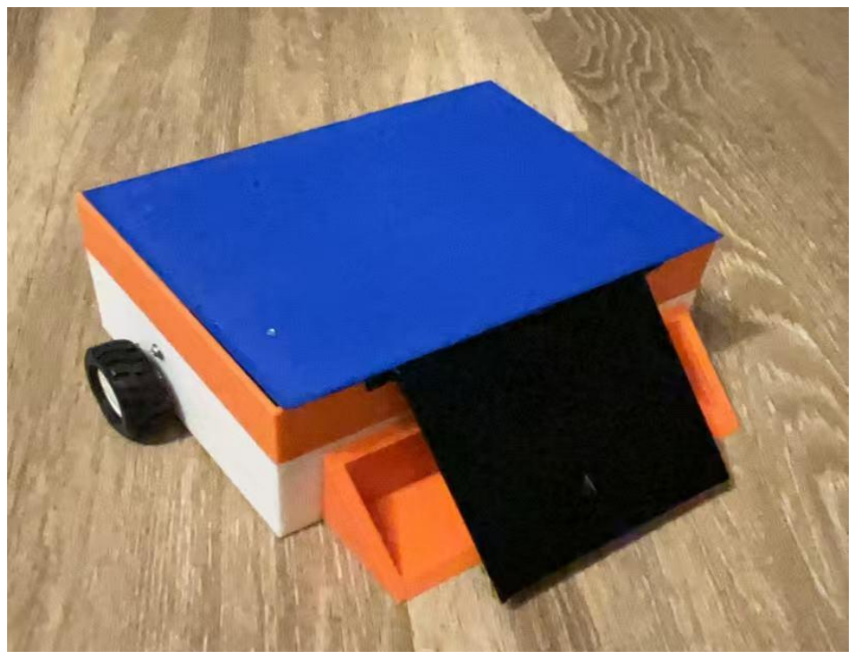
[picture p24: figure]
CHART / GRAPH

The final design of our battlebot! Current score for this battlebot: 1 win - 1 loss.

## Let’s see what is our battlebot looks like

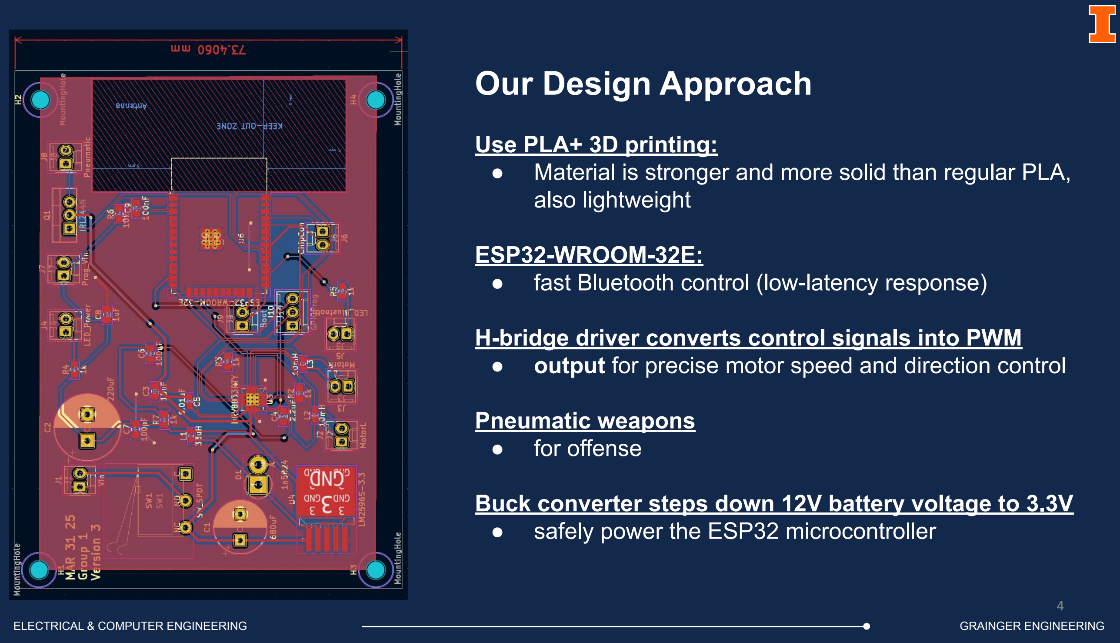
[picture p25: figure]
IMAGE; Our Design Approach; Use PLA+ 3D printing:; also lightweight; ESP32-WROOM-32E:; Pneumatic weapons ● for offense

- Material is stronger and more solid than regular PLA,
- fast Bluetooth control (low-latency response)

H-bridge driver converts control signals into PWM
- output for precise motor speed and direction control

Buck converter steps down 12V battery voltage to 3.3V
- safely power the ESP32 microcontroller

## Let’s see what inside our battlebot

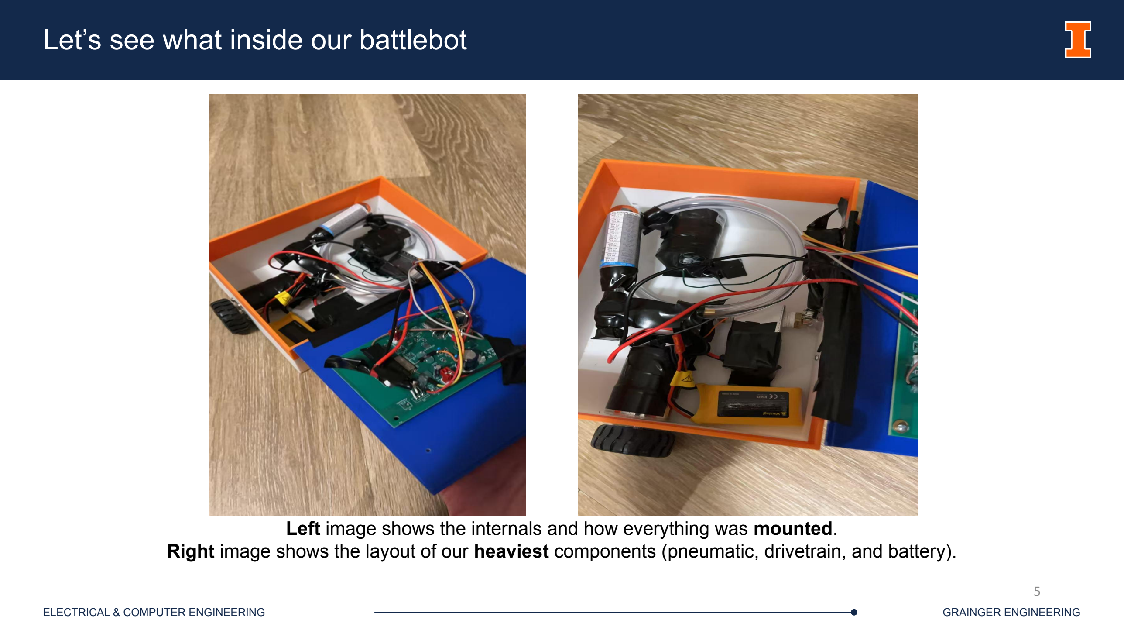
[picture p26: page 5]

Left image shows the internals and how everything was mounted. Right image shows the layout of our heaviest components (pneumatic, drivetrain, and battery).

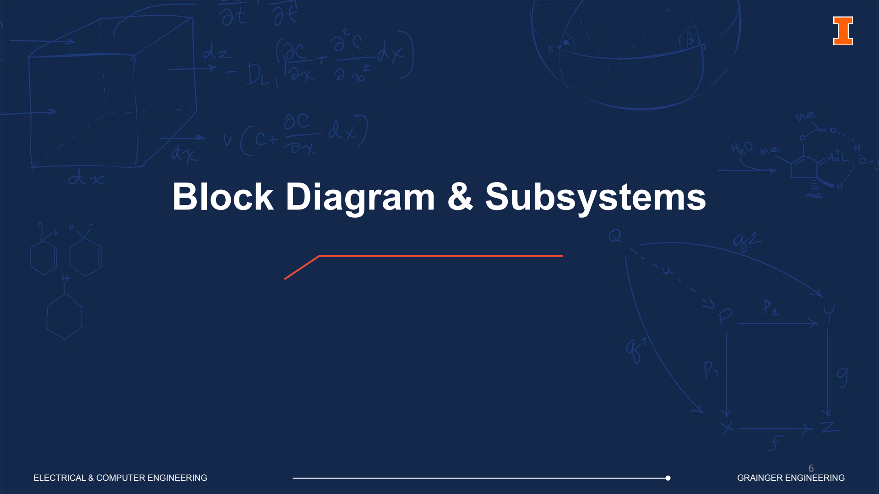
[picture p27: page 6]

# Block Diagram & Subsystems

## Original Block Diagram Design

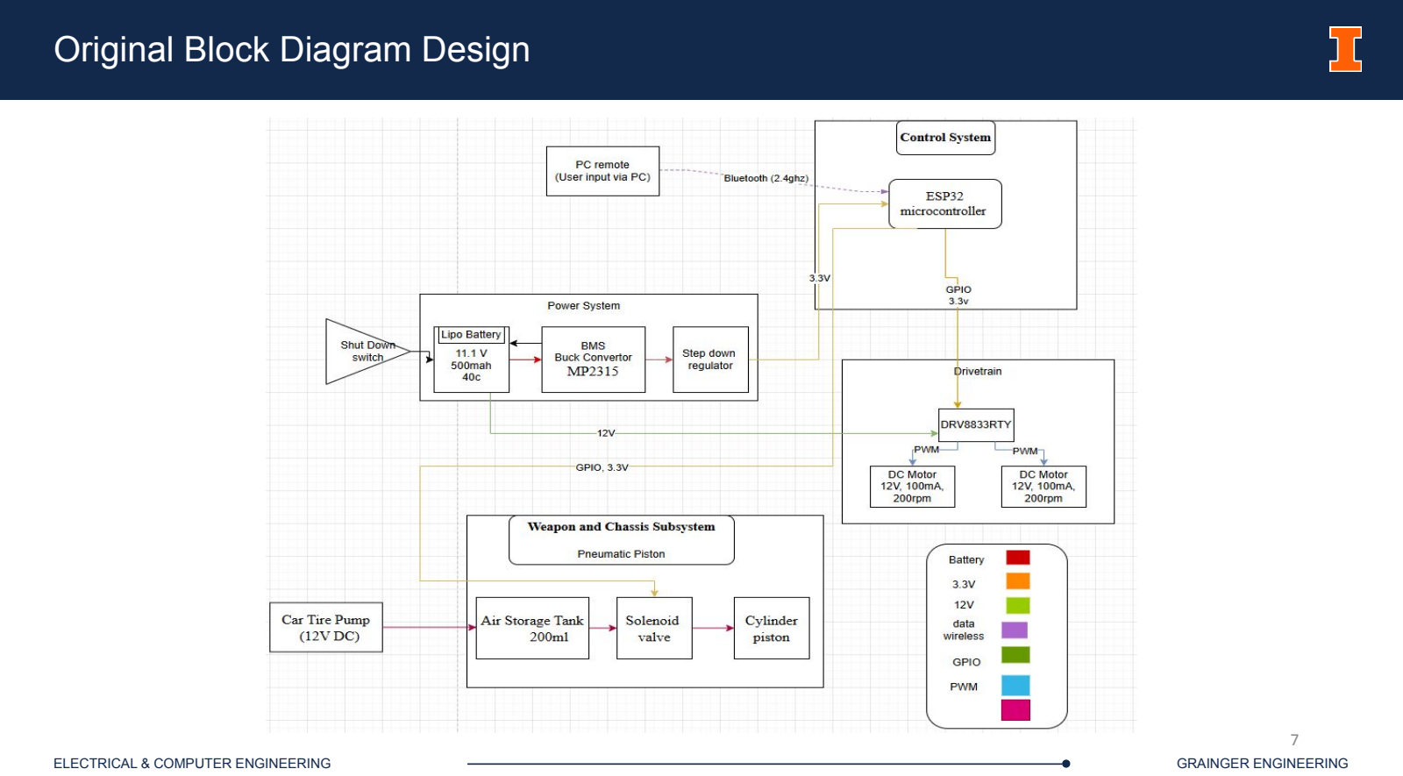
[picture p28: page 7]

CHART / GRAPH

## General Changes for Final Design

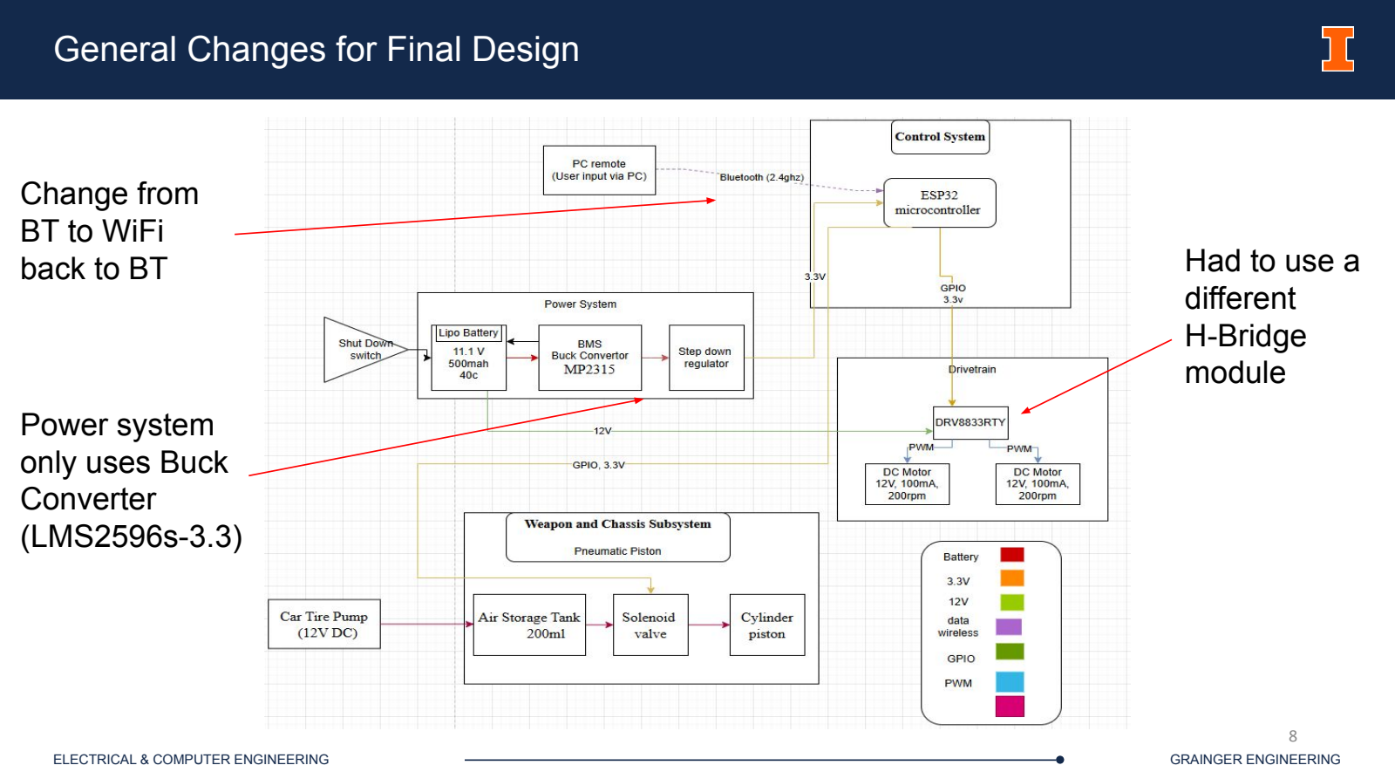
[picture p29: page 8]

CHART / GRAPH

Change from
BT to WiFi
back to BT

Power system
only uses Buck
Converter
(LMS2596s-3.3)

Had to use a
different
H-Bridge
module

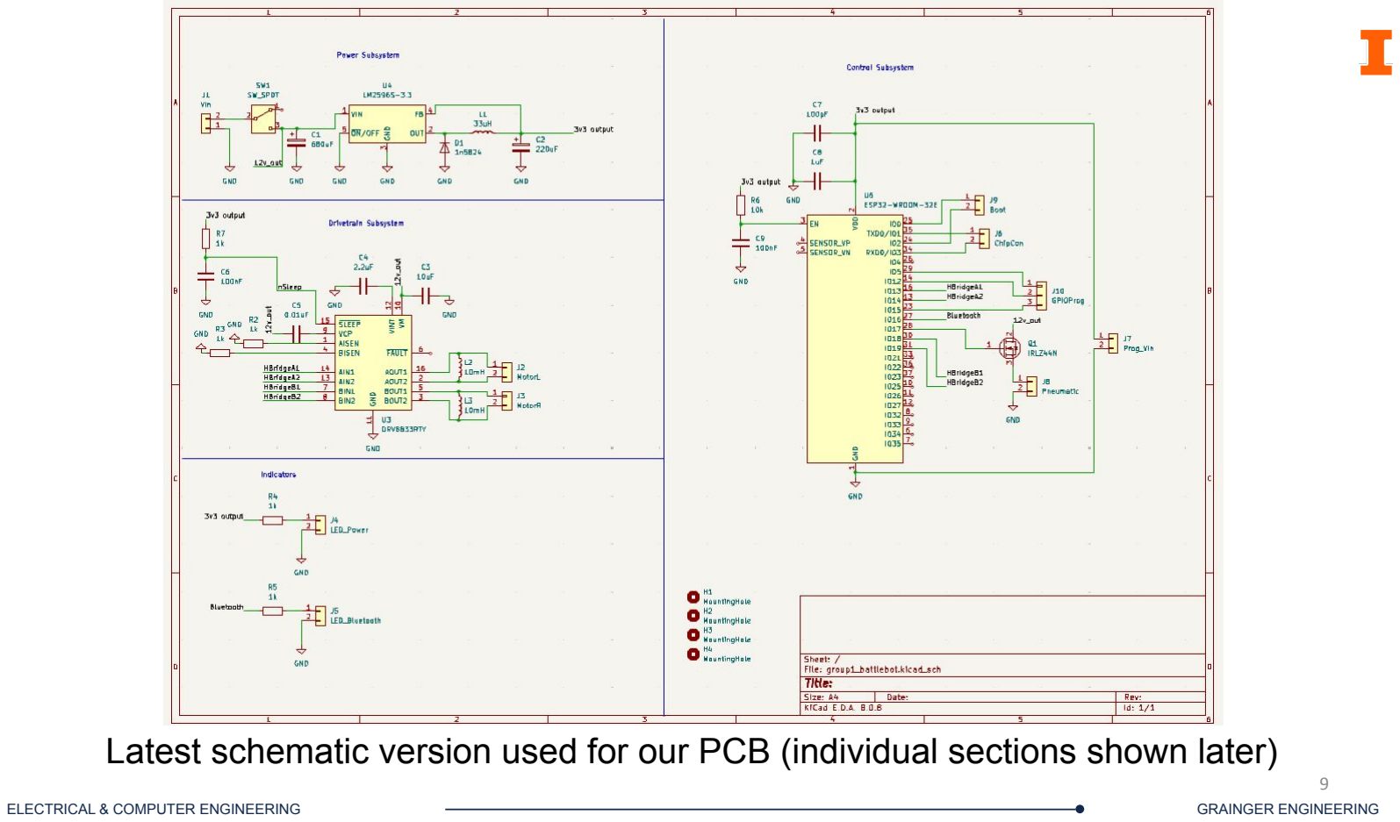
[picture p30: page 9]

IMAGE (Send to back so Block I is not covered.)

### Latest schematic version used for our PCB (individual sections shown later)

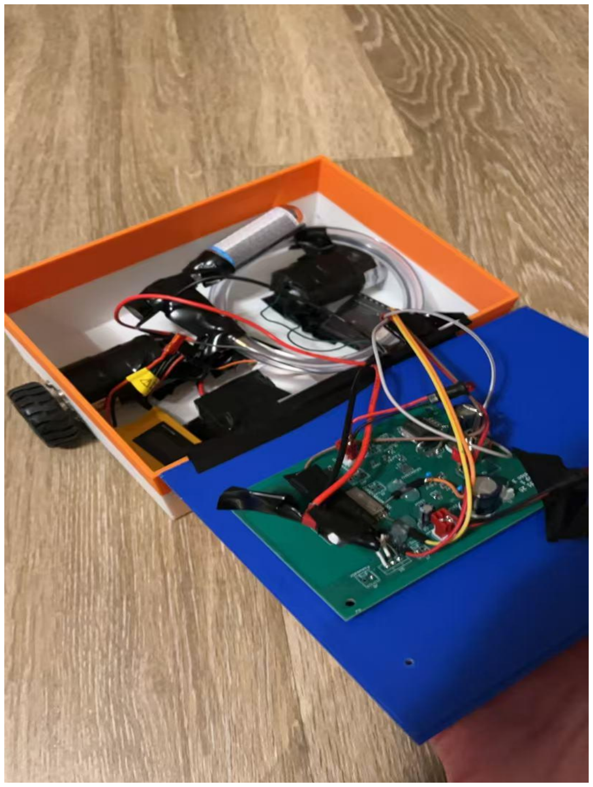
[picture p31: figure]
IMAGE / GRAPHIC

- Uses Bluetooth with a response time of under 100ms.
- Drivetrain uses two high-torque DC motors powered by an H-bridge circuit for precise movement and speed control.
- Skid Bucket weapon controlled via a pneumatic actuator, capable of flipping or destabilizing 2 lb opponents.
- 3D-printed chassis using PLA+ plastic, ensuring durability and stability.
- Utilize a 3S 11.1V 500mAh LiPo battery with proper protections

## High Level Requirement Table

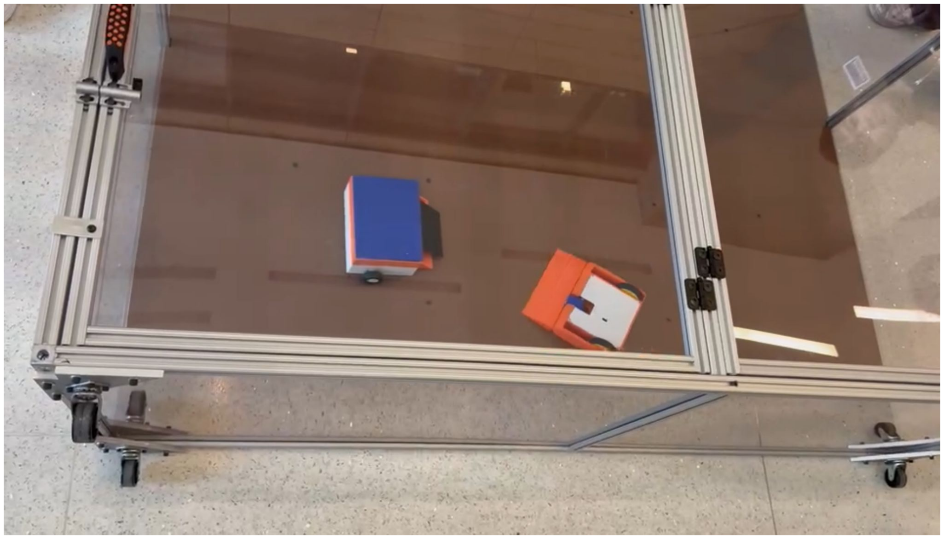
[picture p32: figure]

### A short clip of our functioning robot!

Functional Video (https://youtu.be/LQH7uXVlK6E)
Round 1 Fight! (https://www.youtube.com/shorts/OFhTFmvBGHI)

- Utilized two high torque DC motors from Greartisan
- Each provides 2.2kg*cm of torque with no-load speed of 200 rpm
- Note: Originally, utilized an H-bridge from Texas Instruments, the DRV8833RTY
- However, due to how we wired original circuit, we fried 3 of these chips since we were giving 12V to an H-bridge with maximum 10.8V
- Ended up using a L9110s DC motor driver module
- “Sticky tires” – most amount of grip to complement the high torque DC motors
- Side Note: Peak current draw is 1A with an average of 0.3A

## Subsystem: Drivetrain

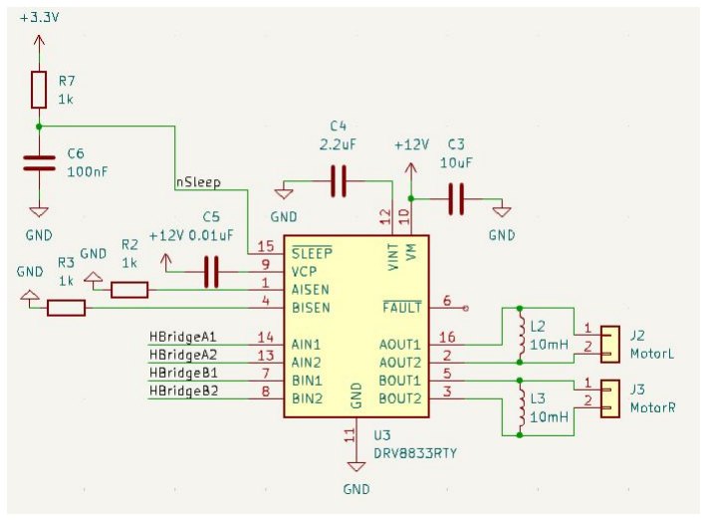
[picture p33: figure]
IMAGE / GRAPHIC

## Subsystem: Drivetrain, Requirements & Verification

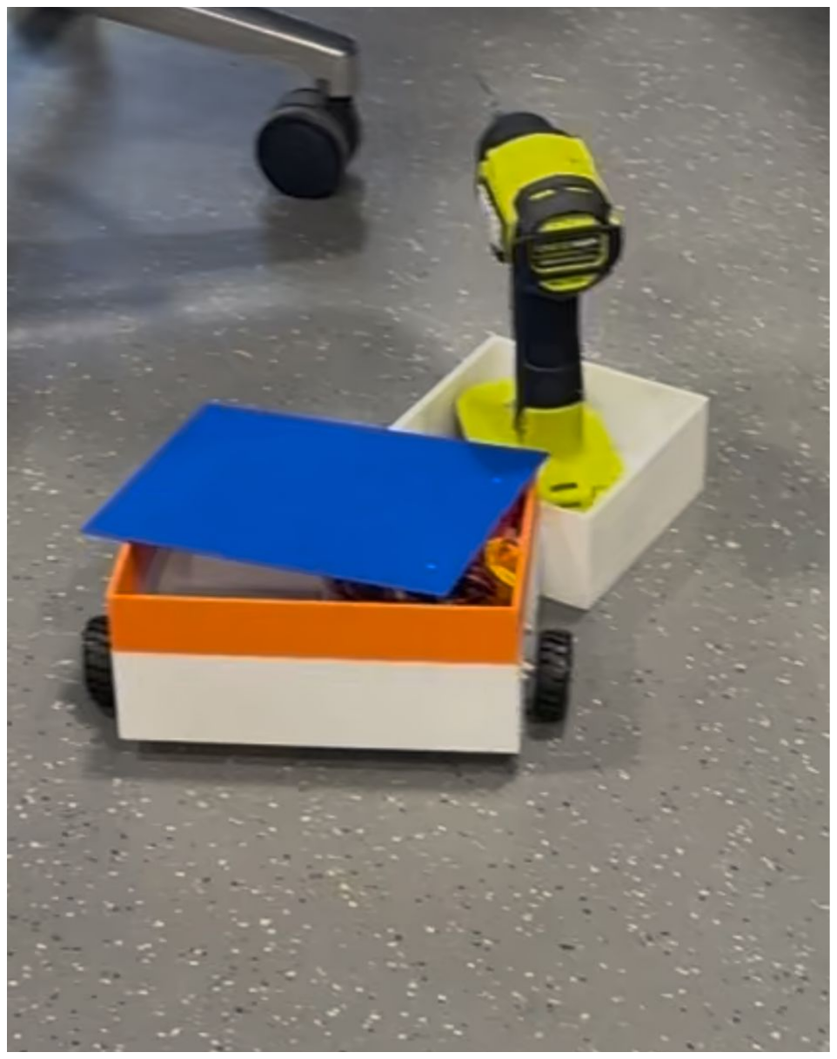
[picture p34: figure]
IMAGE / GRAPHIC

Requirements | Verification
Can produce a maximum of 2.2kg*cm of torque under no load | ● Tested by pushing something of 2.2kg for approx. 1cm ● Ended up using the battlebot to push something of roughly 4lbs (close to 2.2kg) with our final battlebot
Can reach a maximum of 210 rpm under no load | ● We did not have a tachometer, counted revolutions and approximated the rpm ● Roughly 210 rpm (3.5 revolutions per second)

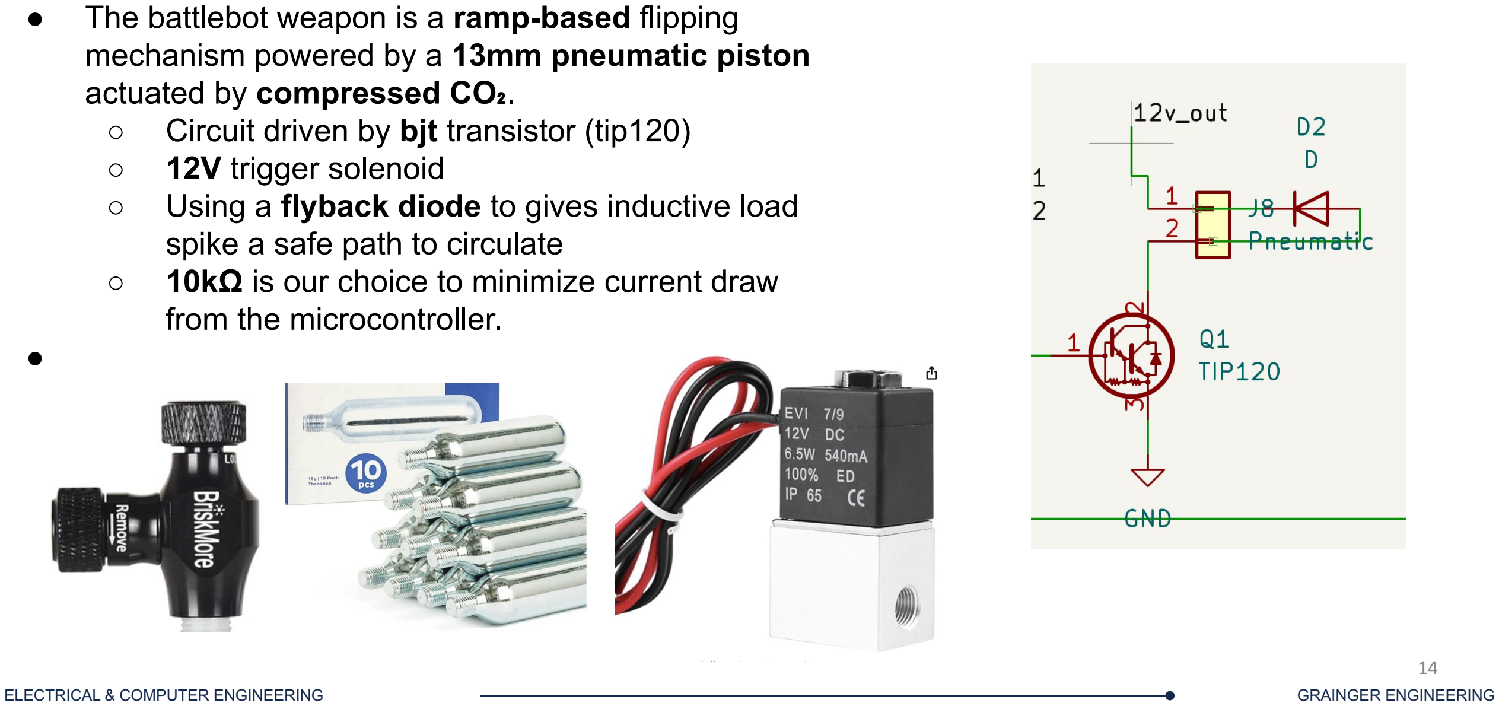
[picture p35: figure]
IMAGE / GRAPHIC; actuated by compressed CO₂.; ○ 12V trigger solenoid; spike a safe path to circulate; from the microcontroller.

- The battlebot weapon is a ramp-based flipping mechanism powered by a 13mm pneumatic piston
- Circuit driven by bjt transistor (tip120)
- Using a flyback diode to gives inductive load
- 10kΩ is our choice to minimize current draw

## Subsystem: Weapon (of Weapon/Chassis)

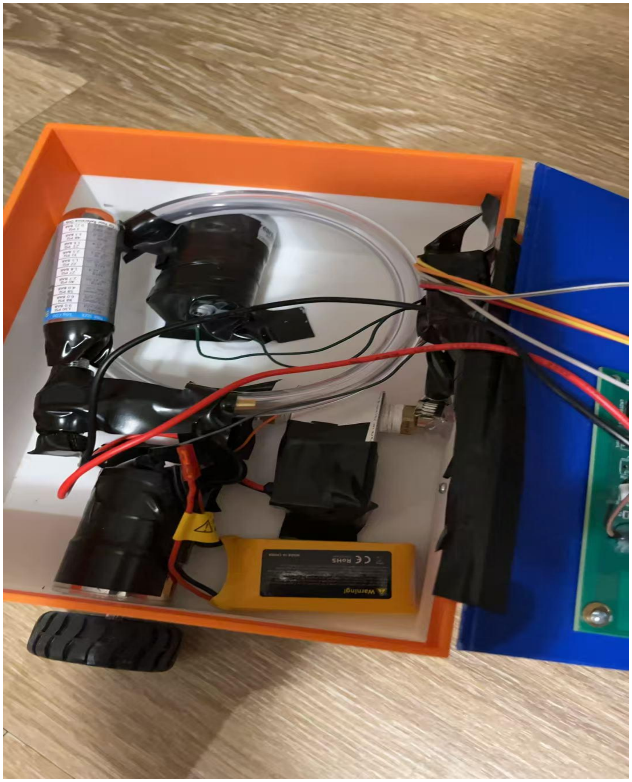
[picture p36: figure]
IMAGE / GRAPHIC

- 3D prints utilizing PLA+ plastic served as the main chassis of our Ant-weight battlebot
- PLA+ offers a balance between durability and weight efficiency
- Less brittleness than PLA, also has increased impact resistance
- Mounted most of the heavy components at bottom of chassis
- Lower center of gravity
- Two layers of Ramp and scooper will allow us to slide under the chassis of opponents
- And be able to scoop and ramp under; or use backside of battlebot to ram

## Subsystem: Chassis (of Weapon/Chassis)

## Subsystem: Weapon and Chassis, Requirements & Verification

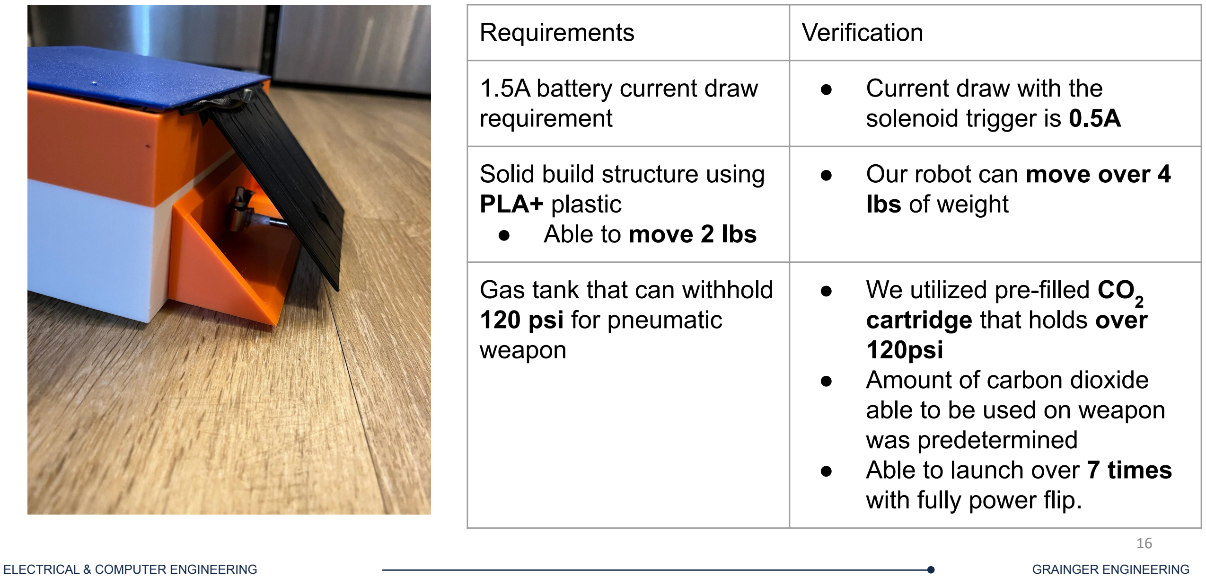
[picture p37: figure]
IMAGE / GRAPHIC; Requirements; Verification; Gas tank that can withhold 120 psi for pneumatic weapon; ● We utilized pre-filled CO2 cartridge that holds over 120psi ● Amount of carbon dioxide able to be used on weapon was predetermined ● Able to launch over 7 times with fully power flip.

1.5A battery current draw requirement | ● Current draw with the solenoid trigger is 0.5A
Solid build structure using PLA+ plastic ● Able to move 2 lbs | ● Our robot can move over 4 lbs of weight

- Relied upon a 11.1V 500mAh LiPo battery
- Max output of approximately 12.6V; used this voltage range of 6-12V for our motors
- Used a buck converter (LM2596S-3.3) to convert 12V to 3.3V
- Allows for use in circuit (Control System)
- Shut off safety: Switch and battery connector to shut off system

## Subsystem: Power System

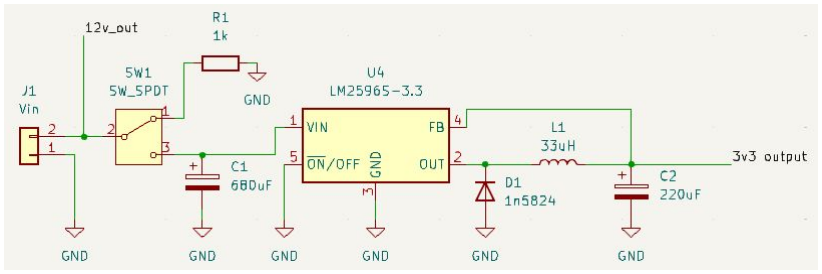
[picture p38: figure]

## Subsystem: Power System, Requirements & Verification

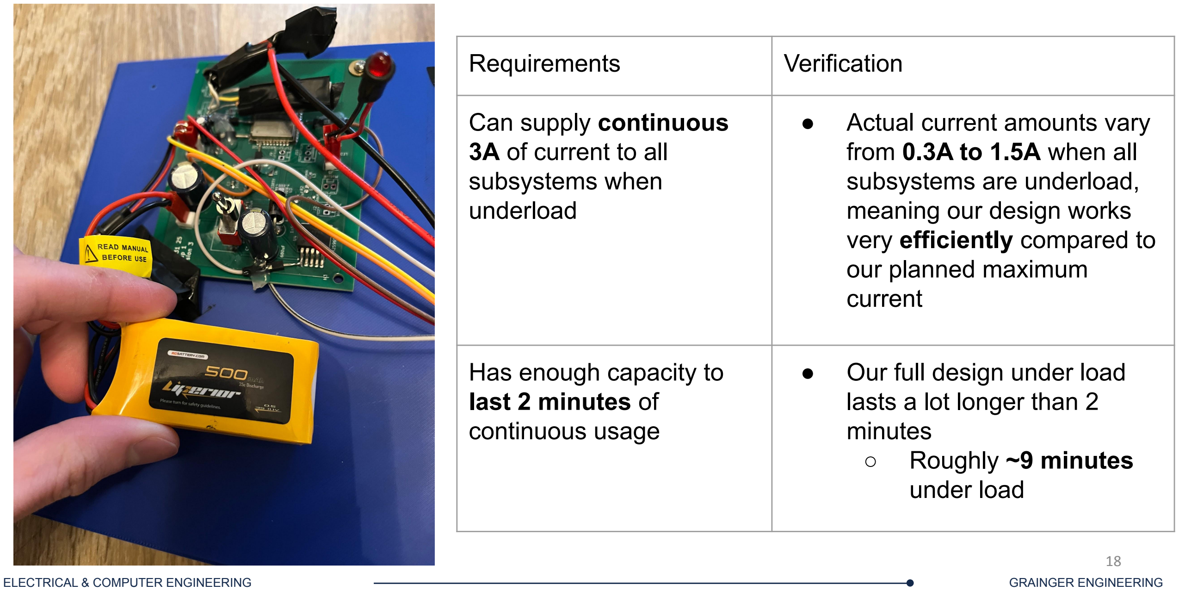
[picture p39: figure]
IMAGE / GRAPHIC; Requirements; Verification; Can supply continuous 3A of current to all subsystems when underload; ● Actual current amounts vary from 0.3A to 1.5A when all subsystems are underload, meaning our design works very efficiently compared to our planned maximum current; Has enough capacity to last 2 minutes of continuous usage; ● Our full design under load lasts a lot longer than 2 minutes ○ Roughly ~9 minutes under load

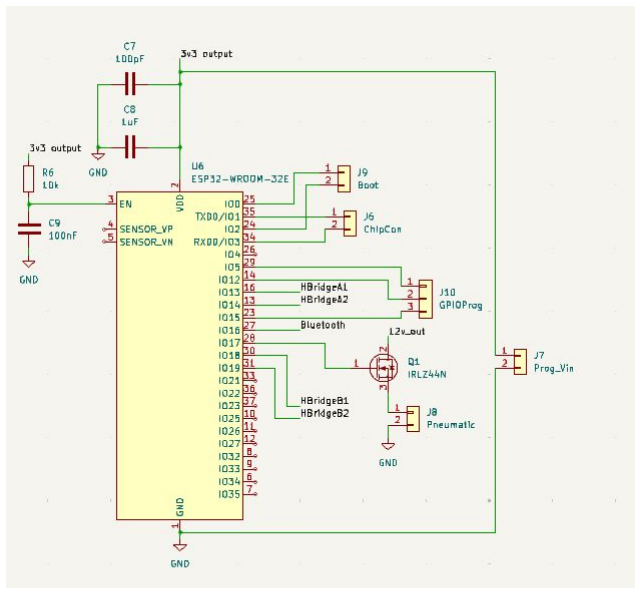
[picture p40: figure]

- Relies on an ESP32-WROOM-32E as our central processing unit
- Uses Bluetooth connectivity
- (Originally wanted WiFi)
- Can leverage PWM and GPIO for control of motors (drivetrain) and Pneumatic (weapon) systems

## Subsystem: Control System

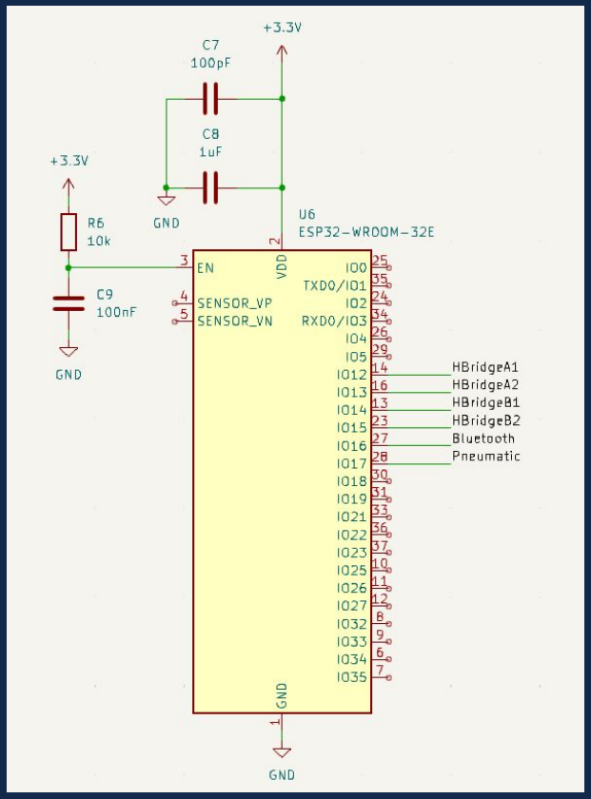
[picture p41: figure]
IMAGE

Original design of our Control System!

## Subsystem: Control System, Requirements & Verification

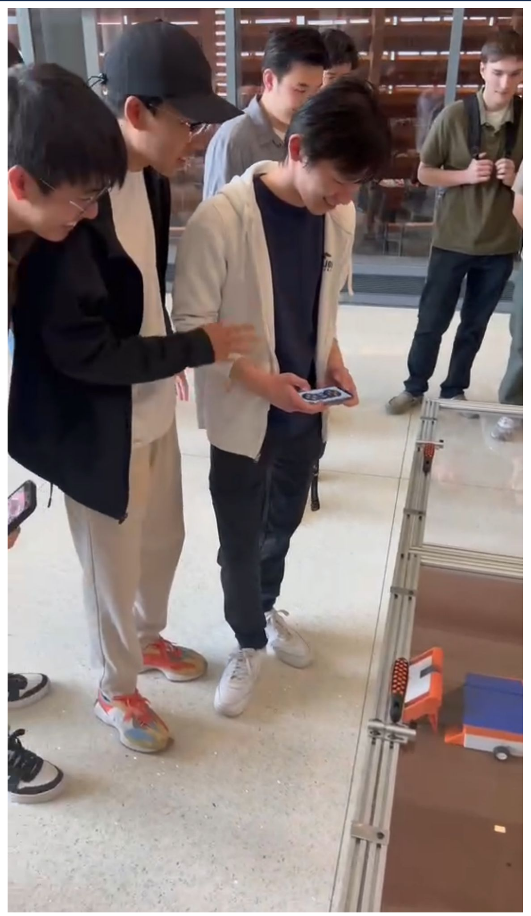
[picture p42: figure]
IMAGE / GRAPHIC

Requirements | Verification
Connect via Bluetooth | ● Able to use phone to connect to Battlebot ● Utilize Dabble library to connect ● LED to display bluetooth is in use
Be able to control all 4 directional movements of battlebot with given signals - left, right, forward, backwards | ● Able to move in the 4 directions properly ● H Bridge A1,A2,B1,B2

Average and Peak Current Draw of both motors:

Imotors = Nmotors * Imotor = 2 * 0.1A = 0.2A

IpeakM = Nmotors * Imotor_peak = 2 * 2A = 4A

Total and Peak Current Draws:
I

total = Imotors + Ipneumatic + IIC = 0.2A + 3A + 0.15A = 3.35A

Ipeak = Imotors_peak + Ipneumatic_peak + IIC_peak = 4A + 5A + 0.2A = 9.2A

Capacity of Battery Wanted = Itotal * Total Time = 3.35A * 2min = 3.35 * 2/60 h = 0.1116 Ah
Peak current of battery = 9.2A

(3.35A/500mAh = 6.7C and 9.2A/500mAh = 18.4C), both of which are within discharge rate limits of our battery: 6.7C < 35C and 18.4C < 70C

## Original Tolerance Analysis Calculations

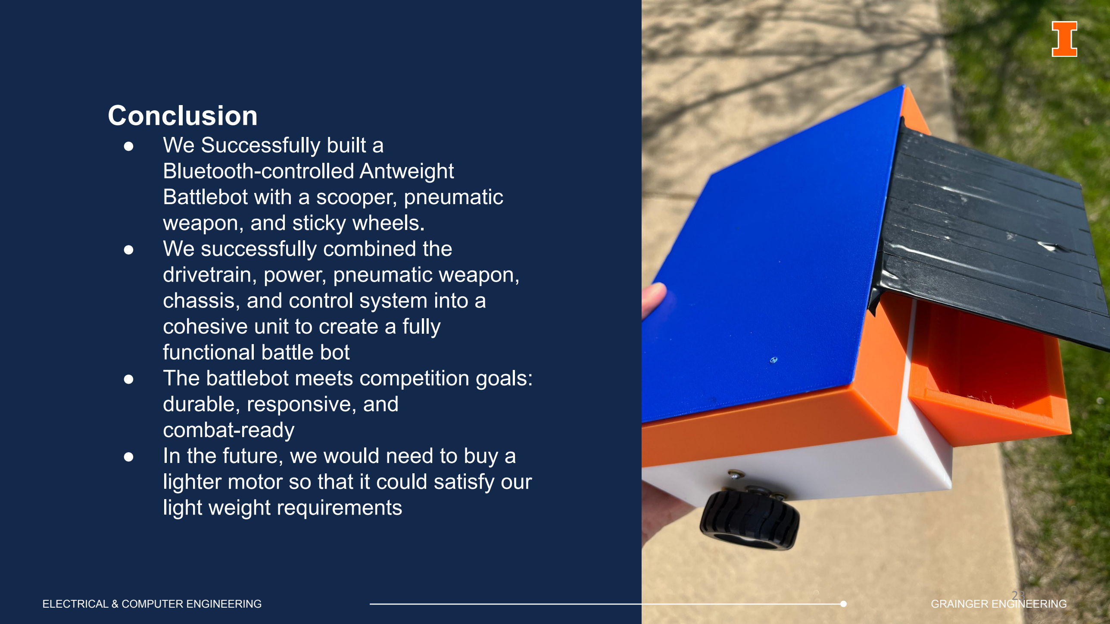
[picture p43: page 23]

Conclusion ● | We Successfully built a
| Bluetooth-controlled Antweight Battlebot with a scooper, pneumatic weapon, and sticky wheels.
- We successfully combined the
| drivetrain, power, pneumatic weapon, chassis, and control system into a cohesive unit to create a fully functional battle bot
- The battlebot meets competition goals:
| durable, responsive, and combat-ready
- In the future, we would need to buy a
| lighter motor so that it could satisfy our light weight requirements
ELECTRICAL & COMPUTER ENGINEERING | GRAINGER ENGINEERING 23

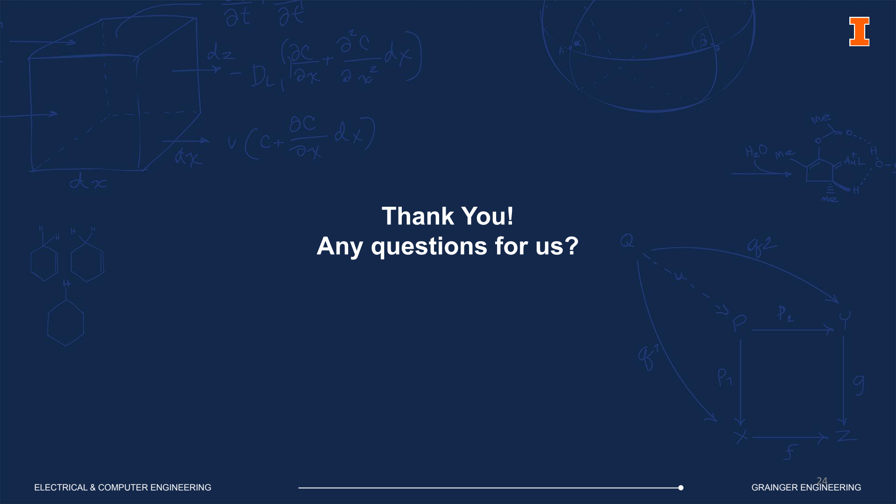
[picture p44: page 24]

## Thank You! Any questions for us?

ELECTRICAL & COMPUTER ENGINEERING | GRAINGER ENGINEERING 24

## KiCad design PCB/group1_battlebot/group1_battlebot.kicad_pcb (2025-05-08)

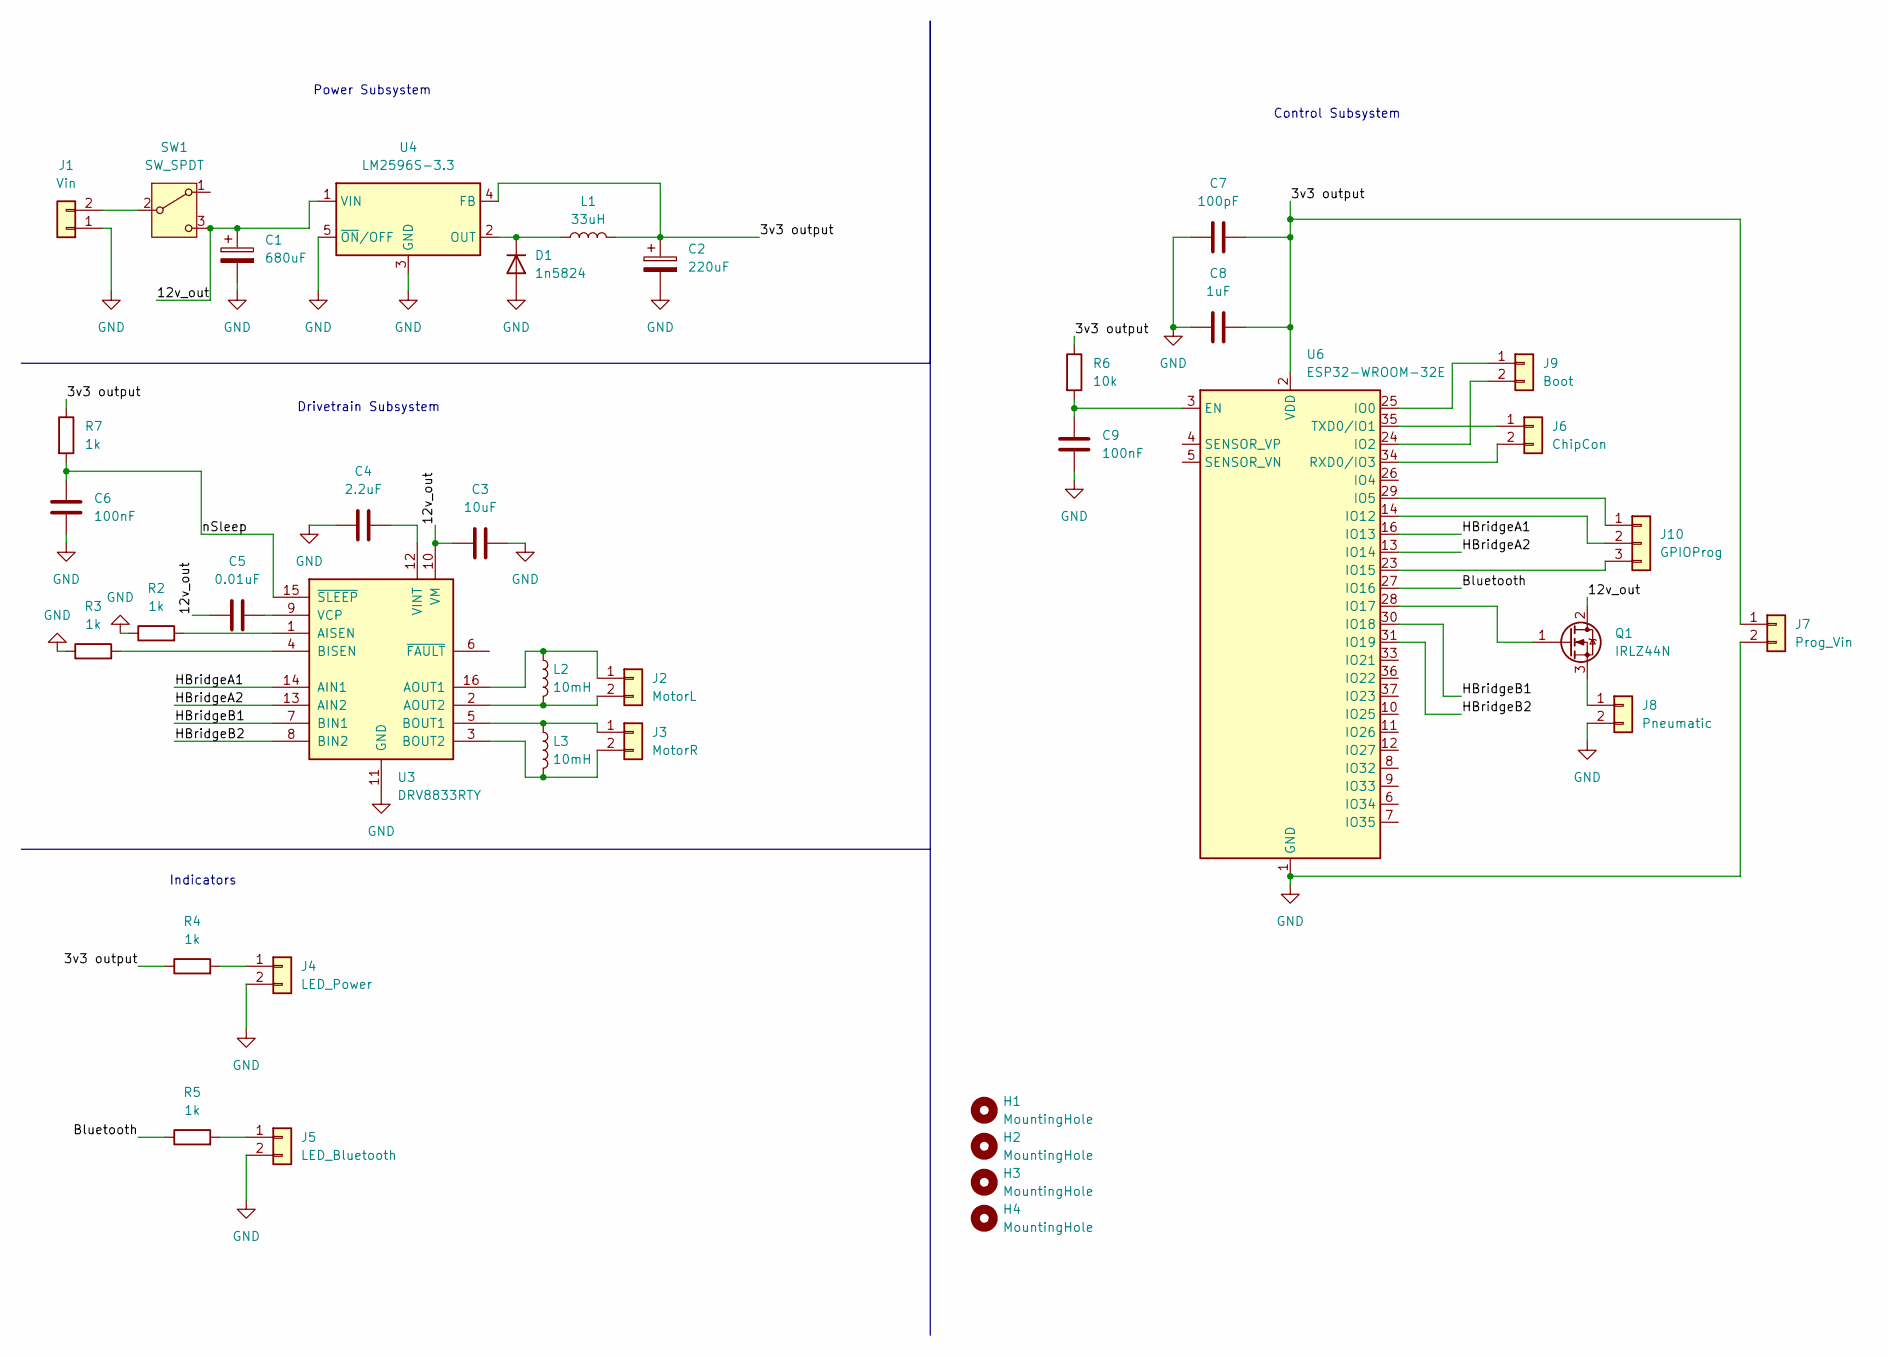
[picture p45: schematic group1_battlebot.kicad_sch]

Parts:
C1: 680uF; CP_Radial_D10.0mm_P5.00mm
C2: 220uF; CP_Radial_D12.5mm_P5.00mm
C3: 10uF; C_0805_2012Metric_Pad1.18x1.45mm_HandSolder
C4: 2.2uF; C_0805_2012Metric_Pad1.18x1.45mm_HandSolder
C5: 0.01uF; C_0603_1608Metric_Pad1.08x0.95mm_HandSolder
C6, C9: 100nF; C_0805_2012Metric_Pad1.18x1.45mm_HandSolder
C7: 100pF; C_0805_2012Metric_Pad1.18x1.45mm_HandSolder
C8: 1uF; C_0805_2012Metric_Pad1.18x1.45mm_HandSolder
D1: 1n5824; D_DO-201AD_P3.81mm_Vertical_AnodeUp
H1, H2, H3, H4: MountingHole; MountingHole_3.2mm_M3
J1: Vin; Molex_KK-254_AE-6410-02A_1x02_P2.54mm_Vertical
J2: MotorL; Molex_KK-254_AE-6410-02A_1x02_P2.54mm_Vertical
J3: MotorR; Molex_KK-254_AE-6410-02A_1x02_P2.54mm_Vertical
J4: LED_Power; Molex_KK-254_AE-6410-02A_1x02_P2.54mm_Vertical
J5: LED_Bluetooth; Molex_KK-254_AE-6410-02A_1x02_P2.54mm_Vertical
J6: ChipCon; Molex_KK-254_AE-6410-02A_1x02_P2.54mm_Vertical
J7: Prog_Vin; Molex_KK-254_AE-6410-02A_1x02_P2.54mm_Vertical
J8: Pneumatic; Molex_KK-254_AE-6410-02A_1x02_P2.54mm_Vertical
J9: Boot; Molex_KK-254_AE-6410-02A_1x02_P2.54mm_Vertical
J10: GPIOProg; Molex_KK-254_AE-6410-03A_1x03_P2.54mm_Vertical
L1: 33uH; L_0603_1608Metric_Pad1.05x0.95mm_HandSolder
L2, L3: 10mH; L_0603_1608Metric_Pad1.05x0.95mm_HandSolder
Q1: IRLZ44N; TO-220-3_Vertical
R2, R3, R4, R5, R7: 1k; R_0805_2012Metric_Pad1.20x1.40mm_HandSolder
R6: 10k; R_0805_2012Metric_Pad1.20x1.40mm_HandSolder
SW1: SW_SPDT; SW_XKB_DM1-16UD-1
U3: DRV8833RTY; Texas_RTY_WQFN-16-1EP_4x4mm_P0.65mm_EP2.1x2.1mm_ThermalVias
U4: LM2596S-3.3; TO-263-5_TabPin3
U6: ESP32-WROOM-32E; ESP32-WROOM-32D

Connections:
/3v3 output: C2.1, C7.2, C8.1, J7.1, L1.2, R4.1, R6.1, R7.1, U4.4 (FB), U6.2 (VDD)
/12v_out: C1.1, C3.2, C5.1, Q1.2 (D), SW1.3 (C), U3.10 (VM), U4.1 (VIN)
/Bluetooth: R5.1, U6.27 (IO16)
/HBridgeA1: U3.14 (AIN1), U6.16 (IO13)
/HBridgeA2: U3.13 (AIN2), U6.13 (IO14)
/HBridgeB1: U3.7 (BIN1), U6.30 (IO18)
/HBridgeB2: U3.8 (BIN2), U6.31 (IO19)
/nSleep: C6.2, R7.2, U3.15 (~SLEEP)
GND: C1.2, C2.2, C3.1, C4.1, C6.1, C7.1, C8.2, C9.1, D1.2 (A), J1.1, J4.2, J5.2, J7.2, J8.2, R2.1, R3.1, U3.11 (GND), U3.17 (GND), U4.3 (GND), U4.5 (~ON/OFF), U6.1 (GND), U6.15 (GND), U6.38 (GND), U6.39 (GND)
unnamed: D1.1 (K), L1.1, U4.2 (OUT)
unnamed: J1.2, SW1.2 (B)
unnamed: J2.1, L2.1, U3.16 (AOUT1)
unnamed: J2.2, L2.2, U3.2 (AOUT2)
unnamed: J3.1, L3.1, U3.5 (BOUT1)
unnamed: J3.2, L3.2, U3.3 (BOUT2)
unnamed: J4.1, R4.2
unnamed: J5.1, R5.2
unnamed: J6.1, U6.35 (TXD0/IO1)
unnamed: J6.2, U6.34 (RXD0/IO3)
unnamed: J8.1, Q1.3 (S)
unnamed: J9.1, U6.25 (IO0)
unnamed: J9.2, U6.24 (IO2)
unnamed: J10.1, U6.29 (IO5)
unnamed: J10.2, U6.14 (IO12)
unnamed: J10.3, U6.23 (IO15)
unnamed: Q1.1 (G), U6.28 (IO17)
unnamed: R2.2, U3.1 (AISEN)
unnamed: R3.2, U3.4 (BISEN)
unnamed: C5.2, U3.9 (VCP)
unnamed: C4.2, U3.12 (VINT)
unnamed: C9.2, R6.2, U6.3 (EN)

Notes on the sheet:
Control Subsystem
Indicators
Power Subsystem
Drivetrain Subsystem

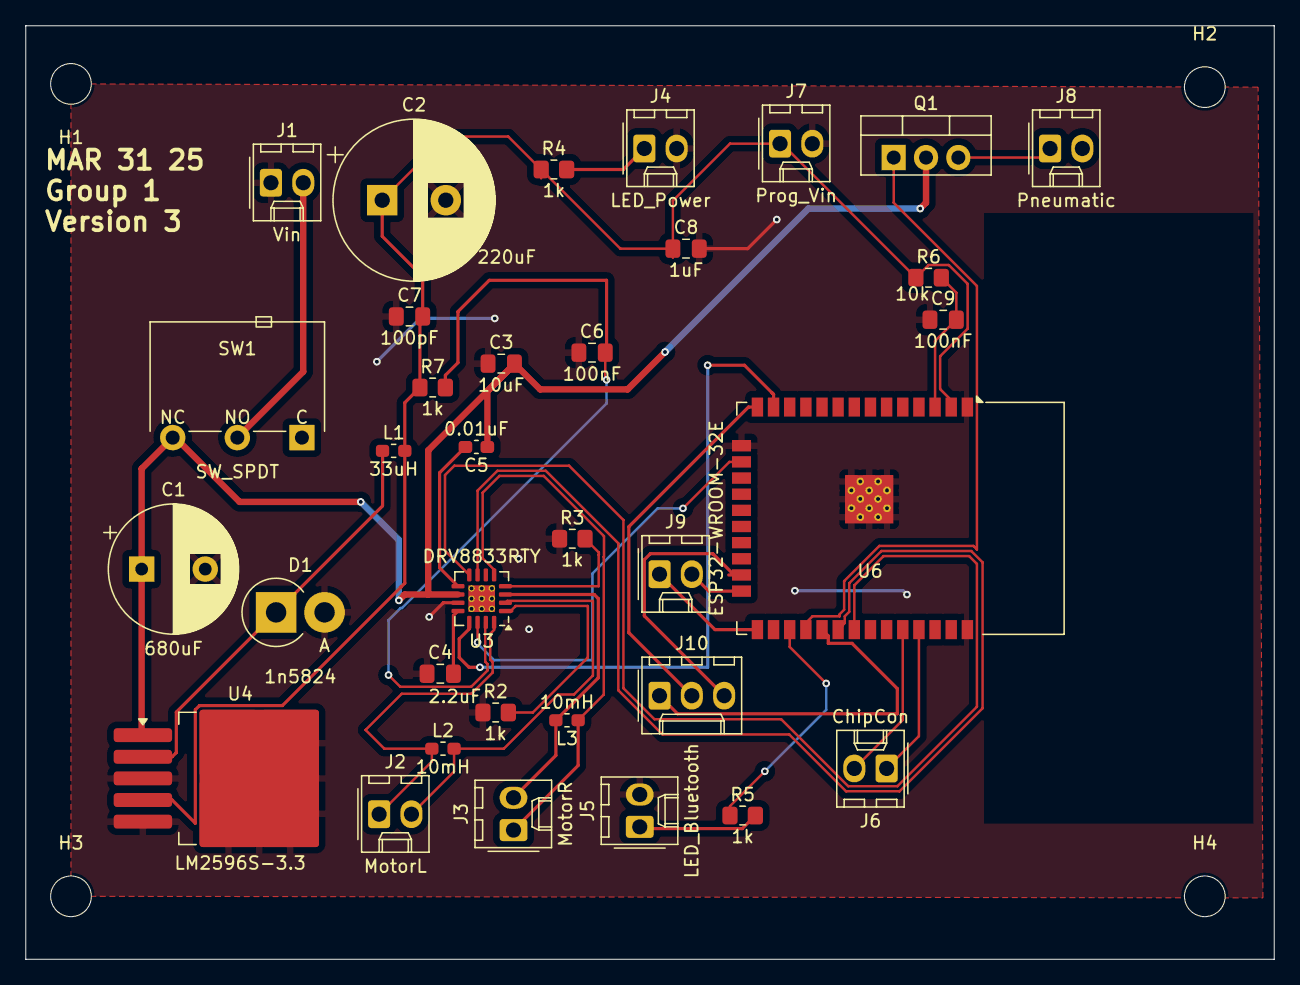
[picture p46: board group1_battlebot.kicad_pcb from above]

Board: 2 copper layers, 98.2 x 73.4 mm, 38 parts (0 on the bottom side), 31 nets.

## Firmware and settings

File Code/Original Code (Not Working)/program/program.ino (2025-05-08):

// #include "link.h"

#include "config.h"
#include "my_wifi.h"
#include "wifi_communicator.h"


// void setup() {
//   // put your setup code here, to run once:
//   Serial.begin(115200);

//   WiFi.begin(ssid,password);


//   Serial.print("Connecting WIFI");
//   while (WiFi.status()!= WL_CONNECTED)
//   {
//     delay(500);
//     Serial.print(".");
//   }
//   Serial.println("Connected");
//   Serial.print("IP Address: ");
//   Serial.println(WiFi.localIP());
  

//   // WiFi Connect Pin, turn LED on
//   pinMode(WIFI_PIN, OUTPUT);
//   digitalWrite(WIFI_PIN, HIGH);

  
//   // Enable all GPIO
//   pinMode(AIN1_PIN, OUTPUT);
//   pinMode(AIN2_PIN, OUTPUT);
//   pinMode(BIN1_PIN, OUTPUT);
//   pinMode(BIN2_PIN, OUTPUT);
//   pinMode(ATTACK_PIN, OUTPUT);


//   // Test Code
//   // pinMode(TEST_PIN, OUTPUT); // set the pin as output
  
// }


// void loop() {
//   // put your main code here, to run repeatedly:
  
  




//   // Test Code
//   // digitalWrite(TEST_PIN, HIGH);
//   // delay(500);
//   // digitalWrite(TEST_PIN, LOW);
//   // delay(500);

// }




#include <MyButton.h>

#define ENABLE_DEBUG /* <-- Commenting this line will remove any trace of debug printing */
#include <MacroDebugger.h>

#define NUM_LEDS 5
const int LED_PINS[NUM_LEDS] = { AIN1_PIN, AIN2_PIN, BIN1_PIN, BIN2_PIN, PNEUMATIC_PIN };


// Button object to simulate input events
MyButton my_btn(BTN_PIN, NORMAL_DOWN, 50);

// Communication messages
char incoming_msg[MAX_BUFFER_LEN] = {0};
char response[MAX_BUFFER_LEN] = {0};

/* A collection of random responses to send when the button is clicked */
#define NUM_RANDOM_RESPONSES    10
char *responses[NUM_RANDOM_RESPONSES] = {
  "hola!",
  "hiii",
  "potato",
  "arduino",
  "esp32",
  "okay so we get it it's a random message!",
  "so what?",
  "running out of messages here",
  "okay two more to go",
  "finally ..."
};

void setup(){
  DEBUG_BEGIN();
  
  setup_wifi();
  
  setup_wifi_communicator();
  pinMode(LED_PIN, OUTPUT);
  digitalWrite(LED_PIN, HIGH);


  pinMode(AIN1_PIN, OUTPUT);
  pinMode(AIN2_PIN, OUTPUT);
  pinMode(BIN1_PIN, OUTPUT);
  pinMode(BIN2_PIN, OUTPUT);
  pinMode(PNEUMATIC_PIN, OUTPUT);

  DEBUG_I("Done setting up!");
}

void loop(){

  // if we lost connection, we attempt to reconnect (blocking)
  if(!is_client_connected()){
    digitalWrite(LED_PIN, LOW);
    connect_client(); 
    digitalWrite(LED_PIN, HIGH);
  }
  
  bool received = get_message(incoming_msg);

  if(received){
    DEBUG_I("Received: %s", incoming_msg);
    uint8_t start = 0;

    // if(incoming_msg[0] == 'A'){
    //   sprintf(response, "%s", ACK);
    //   start++;
    // }

    // //switch the number and do the appropriate action
    // switch(incoming_msg[start]){
    //   case 'n':
    //     digitalWrite(AIN1_PIN, HIGH);
    //     break;

    //   default:
    //   case 'f':
    //     digitalWrite(AIN1_PIN, LOW);
    //     break;
    // }

    int btn_index = incoming_msg[0] - '0';  // Convert ASCII to integer
    char state = incoming_msg[1];  // Get 'n' or 'f' state

    // Validate button index
    if (btn_index >= 0 && btn_index < NUM_LEDS) {
      if (state == 'n') {
        digitalWrite(LED_PINS[btn_index], HIGH);
      } else if (state == 'f') {
        digitalWrite(LED_PINS[btn_index], LOW);
      }
    }


    // If start is bigger than 0, then we have to acknowledge the reception
    if(start > 0){
      send_message(response);
      // Clear the response buffer
      memset(response, 0, MAX_BUFFER_LEN);
    }
  }

  if(my_btn.readRisingClick()){
    // Choose a random response to send back
    uint8_t idx = random(NUM_RANDOM_RESPONSES);
    strncpy(response, responses[idx], MAX_BUFFER_LEN);
    send_message(response);
    memset(response, 0, MAX_BUFFER_LEN);
    DEBUG_I("Sent: %s", responses[idx]);
  }
}

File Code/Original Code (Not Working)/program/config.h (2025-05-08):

#ifndef __CONFG_H___
#define __CONFG_H___

/* Pins definitions */

#define AIN1_PIN                    37
#define AIN2_PIN                    36
#define BIN1_PIN                    35
#define BIN2_PIN                    45
#define PNEUMATIC_PIN               9
#define LED_PIN                     38
#define BTN_PIN                     25 // Useless

// // GPIO setup
// #define AIN1_PIN      14
// #define AIN2_PIN      26
// #define BIN1_PIN      27
// #define BIN2_PIN      32
// #define ATTACK_PIN    33    // Pneumatic
// #define WIFI_PIN      27    // Original was Bluetooth


/* Communication params */
#define ACK                         "A" // acknowledgment packet
#define QUEUE_LEN                   5
#define MAX_BUFFER_LEN              128

/* WiFi params */
#define WIFI_SSID                   "Yuxuan S24"
#define WIFI_PASSWORD               "qwertyui"

/* Socket */
#define SERVER_ADDRESS              "192.168.107.188" //"PYTHON.IP.GOES.HERE"
#define SERVER_PORT                 11111

#endif // __CONFG_H___

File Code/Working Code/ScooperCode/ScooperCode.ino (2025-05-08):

#define CUSTOM_SETTINGS
#define INCLUDE_GAMEPAD_MODULE
#include <DabbleESP32.h>

// Code for helping change actual Dabble libraries to work on current ESP32 core
// #if ESP_IDF_VERSION >= ESP_IDF_VERSION_VAL(5, 1, 1)
//   ledcAttach(LED_BUILTIN, 5000, 8);
// #else
//   ledcSetup(0, 5000, 8);
//   ledcAttachPin(LED_BUILTIN, 0);
// #endif


// INITIALIZING VARIABLES
// ESP32-S3 Version (Fried)
// int EN1 = 37;     // MOTOR 1 CONNECTIONS 
// int EN2 = 38;     // MOTOR 2 CONNECTIONS
// int EN3 = 36;     // MOTOR 3 CONNECTIONS
// int EN4 = 39;     // MOTOR 4 CONNECTIONS
// int PNE = 40;     // PNEUMATICS

// ESP32
// int EN1 = 4; // HBridge A1
// int EN2 = 16; // HBridge A2
// int EN3 = 17; // HBridge B1
// int EN4 = 5; // HBridge B2
// int PNE = 18; // Pneumatic
// int BLE = 19; // Bluetooth LED

// ESP32 Bare Chip
int EN1 = 13; // HBridge A1
int EN2 = 14; // HBridge A2
// int EN3 = 18; // HBridge B1
int EN3 = 32; // HBridge B1
int EN4 = 19; // HBridge B2
int PNE = 17; // Pneumatic
int BLE = 16; // Bluetooth LED




void setup() {
  // put your setup code here, to run once:
  Serial.begin(115200);      // make sure your Serial Monitor is also set at this baud rate.
  Dabble.begin("Scooper");       //set bluetooth name of your device

  Serial.println("ROBOT CAR..\n\n");
  pinMode(EN1, OUTPUT);  // MOTOR 1 AS OUTPUT
  pinMode(EN2, OUTPUT);  // MOTOR 2 AS OUTPUT
  pinMode(EN3, OUTPUT);  // MOTOR 3 AS OUTPUT
  pinMode(EN4, OUTPUT);  // MOTOR 4 AS OUTPUT
  pinMode(PNE, OUTPUT);  // Pneumatic AS OUTPUT
  pinMode(BLE, OUTPUT);  // Bluetooth
  digitalWrite(BLE, HIGH);
  

}

void loop() {
  Dabble.processInput();             //this function is used to refresh data obtained from smartphone.Hence calling this function is mandatory in order to get data properly from your mobile.
  Serial.print("KeyPressed: ");

  // Move up
  if (GamePad.isUpPressed())
  {
    Serial.print("Up");
    Serial.println(" ROBOT CAR MOVING FORWARD...");
    // digitalWrite(EN1, HIGH);
    // delay(200);
    // digitalWrite(EN1, LOW);
    digitalWrite(EN1, HIGH); // AIN1 = 1
    digitalWrite(EN3, HIGH); // BIN1 = 1
    digitalWrite(EN2, LOW); // AIN2 = 0
    digitalWrite(EN4, LOW); // BIN2 = 0
    delay(200);
    digitalWrite(EN1, LOW);
    digitalWrite(EN3, LOW);

  }

  if (GamePad.isDownPressed())
  {
    Serial.print("Down");
    Serial.println(" ROBOT CAR MOVING BACKWARD...");
    // digitalWrite(EN2, HIGH);
    // delay(200);
    // digitalWrite(EN2, LOW);
    digitalWrite(EN1, LOW); // AIN1 = 0
    digitalWrite(EN3, LOW); // BIN1 = 0
    digitalWrite(EN2, HIGH); // AIN2 = 1
    digitalWrite(EN4, HIGH); // BIN2 = 1
    delay(200);
    digitalWrite(EN2, LOW);
    digitalWrite(EN4, LOW);

  }

  if (GamePad.isLeftPressed())
  {
    Serial.print("Left");
    Serial.println(" ROBOT CAR MOVING LEFT...");
    // digitalWrite(EN3, HIGH);
    // delay(200);
    // digitalWrite(EN3, LOW);

    // Turn on only right motor
    digitalWrite(EN1, LOW); // AIN1 = 0
    digitalWrite(EN2, LOW); // AIN2 = 0
    digitalWrite(EN3, HIGH); // BIN1 = 1
    digitalWrite(EN4, LOW); // BIN2 = 0
    delay(200);
    digitalWrite(EN3, LOW);

  }

  if (GamePad.isRightPressed())
  {
    Serial.print("Right");
    Serial.println(" ROBOT CAR MOVING RIGHT...");
    // digitalWrite(EN4, HIGH);
    // delay(200);
    // digitalWrite(EN4, LOW);
    digitalWrite(EN1, HIGH); // AIN1 = 1
    digitalWrite(EN2, LOW); // AIN2 = 0
    digitalWrite(EN3, LOW); // BIN1 = 0
    digitalWrite(EN4, LOW); // BIN2 = 0
    delay(200);
    digitalWrite(EN1, LOW);

  }

  if (GamePad.isTrianglePressed() || GamePad.isSquarePressed() || GamePad.isCirclePressed() || GamePad.isCrossPressed())
  {
    Serial.print("Four Button");
    Serial.println(" PNEUMATICS... ");
    digitalWrite(PNE, HIGH);
    delay(400);
    digitalWrite(PNE, LOW);
  }

}

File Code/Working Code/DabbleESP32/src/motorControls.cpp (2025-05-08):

#define FROM_DABBLE_LIBRARY
#include "DabbleESP32.h"
#include "motorControls.h"

int motorControls::minPulseWidth = 544;
int motorControls::maxPulseWidth = 2400;
int motorControls::minAngle = 0;
int motorControls::maxAngle = 180;

	
motorControls::motorControls() : ModuleParent(CONTROLS_ID)
{

}

void motorControls::processData()
{
	   /* #ifdef DEBUG
	    Serial.println("Controls:processData");
		#endif */
		functionId=getDabbleInstance().getFunctionId();
		if(functionId == 0x01 || functionId == 0x02)
		{
			
		byte1=getDabbleInstance().getArgumentData(0)[0]; 
		byte2=getDabbleInstance().getArgumentData(0)[1];
		#ifdef DEBUG
		Serial.print("byte1: ");
		Serial.print(byte1);
		Serial.print("byte2: ");
	    Serial.println(byte2);
		#endif
		if(functionId == 0x01)
		{
			
			if(byte1 == 0xf0)
			{
				pwmMotor1=byte2;
			}
			else if(byte1 == 0xff)
			{
				pwmMotor1= -byte2;
			}
			else if(byte1 == 0x0f)
			{
				pwmMotor1= 0;
			}
			else if(byte1 == 0x00)
			{
				pwmMotor1= 0;
			}
			
		}
		
		if(functionId == 0x02)
		{
			if(byte1 == 0xf0)
			{
				pwmMotor2= byte2;
			}
			else if(byte1 == 0xff)
			{
				pwmMotor2= -byte2;
			}
			else if(byte1 == 0x0f)
			{
				pwmMotor2= 0;
			}
			else if(byte1 == 0x00)
			{
				pwmMotor2= 0;
			}
		}
		}
		else if(functionId == 0x03 || functionId == 0x04)
		{
			byte1=getDabbleInstance().getArgumentData(0)[0]; 
			#ifdef DEBUG
			Serial.print("byte1:");
			Serial.println(byte1);
			#endif
			if(functionId == 0x03)
			{
				angleServo1=byte1;
			}
			else if(functionId == 0x04)
			{
			    angleServo2=byte1;
			}
		}
		
}

void motorControls::runMotor1(uint8_t pwm,uint8_t direction1,uint8_t direction2)
{
	pinMode(direction1,OUTPUT);
	pinMode(direction2,OUTPUT);
	if(prevMotor1pin != pwm)
	{
		// ledcAttachPin(pwm,0);
		// ledcSetup(0,100,8);
		ledcAttach(pwm, 100, 8);
	}
	if(pwmMotor1 > 0)
	{
		digitalWrite(direction1,HIGH);
		digitalWrite(direction2,LOW);
		ledcWrite(0,pwmMotor1);
	}
	else if(pwmMotor1 < 0)
	{
		digitalWrite(direction1,LOW);
		digitalWrite(direction2,HIGH);
		ledcWrite(0,-pwmMotor1);  //making negative pwm value positive
	}
	else
	{
		digitalWrite(direction1,LOW);
		digitalWrite(direction2,LOW);
		ledcWrite(0,0);
	}
	prevMotor1pin = pwm;
}

void motorControls::runMotor2(uint8_t pwm,uint8_t direction1,uint8_t direction2)
{
	pinMode(direction1,OUTPUT);
	pinMode(direction2,OUTPUT);
	if(prevMotor2pin != pwm)
	{
		// ledcAttachPin(pwm,1);
		// ledcSetup(1,100,8);
		ledcAttach(pwm, 100, 8);
	}
	if(pwmMotor2 > 0)
	{

		/*#ifdef DEBUG
		Serial.print(direction1);
		Serial.print(" ");
		Serial.println(direction2);
		Serial.println("Clockwise");
		#endif*/
		digitalWrite(direction1,HIGH);
		digitalWrite(direction2,LOW);
		ledcWrite(1,pwmMotor2);
	}
	else if(pwmMotor2 < 0)
	{
		/*#ifdef DEBUG
		Serial.print(direction1);
		Serial.print(" ");
		Serial.println(direction2);
		Serial.println("Anti-Clockwise");*
		#endif*/
		digitalWrite(direction1,LOW);
		digitalWrite(direction2,HIGH);
		ledcWrite(1,-pwmMotor2);  //making negative pwm value positive
	}
	else
	{
		digitalWrite(direction1,LOW);
		digitalWrite(direction2,LOW);
		ledcWrite(1,0);
	}
	prevMotor2pin = pwm;
}

void motorControls::runServo1(uint8_t pin)    //Attach Servo1 to channel 3
{
	if(prevServo1pin!=pin)
	{
		// ledcAttachPin(pin,3);
		// ledcSetup(3,50,16);
		ledcAttach(pin, 50, 16);
	}
	writeServoAngle(angleServo1,3);
	prevServo1pin = pin;
}

void motorControls::runServo2(uint8_t pin)	 //Attach Servo2 to channel 4
{
    if(prevServo2pin!=pin)
	{
		// ledcAttachPin(pin,4);
		// ledcSetup(4,50,16);
		ledcAttach(pin, 50, 16);
	}
	writeServoAngle(angleServo2,4);
	prevServo2pin = pin;
}

int motorControls::angleTomicroseconds(int degree)
{
	degree = constrain(degree,minAngle,maxAngle);
	return map(degree,minAngle,maxAngle,minPulseWidth,maxPulseWidth);
}

int motorControls::microsecondsToDuty(int pulse)
{
	pulse=constrain(pulse,minPulseWidth,maxPulseWidth);
	return map(pulse,0,20000,0,65535);
}

void motorControls::writeServoAngle(int angle,uint8_t channel)
{
	/*Serial.print(angle);
	Serial.print(" ");
	Serial.println(channel);*/
	int _pulse = angleTomicroseconds(angle);
	int _duty =  microsecondsToDuty(_pulse);
	ledcWrite(channel,_duty);
}

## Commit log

2025-05-08 Added Code and PCB
    [group1_battlebot-B_Cu.gbr, group1_battlebot-B_Mask.gbr, group1_battlebot-B_Paste.gbr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]
2025-05-08 Added Code and PCB important file locations
2025-05-08 Finished Lab Notebook. Also added all the 3D Print files
    [chasis.stl, lid.stl]
2025-05-08 PCB Image
